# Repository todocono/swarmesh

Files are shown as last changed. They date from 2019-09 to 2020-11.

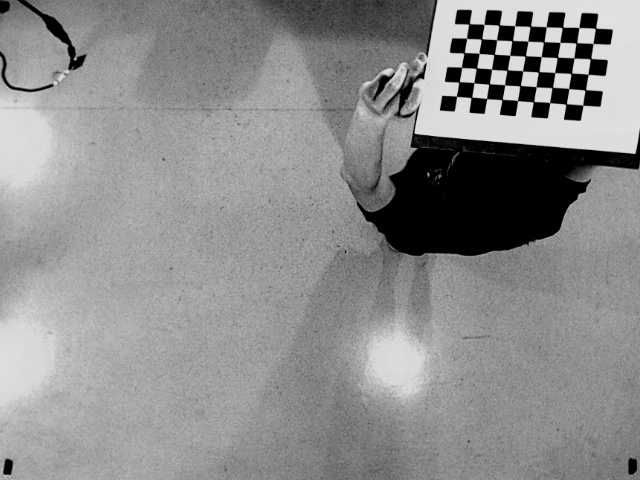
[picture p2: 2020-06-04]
SOFT/testArUco/cam_calib/calib/calib 8.jpg

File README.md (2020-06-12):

# Swarm Mesh Research Team

To read the latest research published by the team, access: 
https://github.com/todocono/DOCS/Publications

To work with the PCB, you will need the latest version of Eagle: https://www.autodesk.com/products/eagle/overview 

To work with the 3D models, you will need Fusion 360 and access the following files:
https://a360.co/2WSIKhr
https://a360.co/2x0crTh

To work with the IDE and latest version, you need:

- Arduino IDE 1.8.9
- CP2102 driver (https://www.silabs.com/products/development-tools/software/usb-to-uart-bridge-vcp-drivers)
- ESP32 Arduino installed 1.0.2 (add https://raw.githubusercontent.com/espressif/arduino-esp32/gh-pages/package_esp32_index.json)
- FastLED library 3.3.2 (from Boards Manager)
- PainlessMesh 1.4.2 (from Boards Manager)
- ArduinoJson 6.12.0 (from Boards Manager)
- TaskScheduler 3.0.2 (from Boards Manager, not really used)
- AsyncTCP (manual install https://github.com/me-no-dev/AsyncTCP)
- AsyncUDP (available in ESP32's arduino library)

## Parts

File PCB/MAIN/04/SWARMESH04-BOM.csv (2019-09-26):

Part | Value | Device | Package | Description | ALLIED_NUMBER | ALLIED_PRICE-STOCK | AVAILABILITY | DESCRIPTION | HEIGHT | MANUFACTURER_NAME | MANUFACTURER_PART_NUMBER | MF | MOUSER_PART_NUMBER | MOUSER_PRICE-STOCK | MP | MPN | OC_FARNELL | OC_NEWARK | PACKAGE | PRICE | RS_PART_NUMBER | RS_PRICE-STOCK | SF_ID
BAT+ |  | PINHD-1X1-BIGPOGO | 1X1-BIGPOGO | Pin header 1x1 for 0.1 spacing"
BAT- |  | PINHD-1X1-BIGPOGO | 1X1-BIGPOGO | Pin header 1x1 for 0.1 spacing"
C1 | 10uF | CPOL-USE2-5 | E2-5 | POLARIZED CAPACITOR, American symbol
C2 |  | C-US025-030X050 | C025-030X050 | CAPACITOR, American symbol
C3 |  | C-US025-025X050 | C025-025X050 | CAPACITOR, American symbol
C4 |  | C-US025-025X050 | C025-025X050 | CAPACITOR, American symbol
C5 |  | C-US025-030X050 | C025-030X050 | CAPACITOR, American symbol
C6 |  | C-US025-025X050 | C025-025X050 | CAPACITOR, American symbol
CHG1+ |  | PINHD-1X1-BIGPOGO | 1X1-BIGPOGO | Pin header 1x1 for 0.1 spacing"
CHG1- |  | PINHD-1X1-BIGPOGO | 1X1-BIGPOGO | Pin header 1x1 for 0.1 spacing"
CHG2+ |  | PINHD-1X1-BIGPOGO | 1X1-BIGPOGO | Pin header 1x1 for 0.1 spacing"
CHG2- |  | PINHD-1X1-BIGPOGO | 1X1-BIGPOGO | Pin header 1x1 for 0.1 spacing"
F1 | RUEF300K-2 | RUEF300K-2 | RUEF300K2 | TE CONNECTIVITY / RAYCHEM - RUEF300K-2 - RESETTABLE FUSE, PTC, 30V, 3A, RADIAL |  |  |  | TE CONNECTIVITY / RAYCHEM - RUEF300K-2 - RESETTABLE FUSE, PTC, 30V, 3A, RADIAL | 16.5mm | TE CONNECTIVITY / RAYCHEM | RUEF300K-2
GPIO25 |  | PINHD-1X3 | 1X03 | PIN HEADER
GPIO26 |  | PINHD-1X3 | 1X03 | PIN HEADER
GPIO32 |  | PINHD-1X3 | 1X03 | PIN HEADER
GPIO33 |  | PINHD-1X3 | 1X03 | PIN HEADER
JI2C |  | PINHD-2X4 | 2X04 | PIN HEADER
JIMU | PINHD-1X10 | PINHD-1X10 | 1X10-BIG | Pin header 1x10 0.1 spacing"
JM1 |  | PINHD-1X6 | 1X06 | PIN HEADER
JM2 |  | PINHD-1X6 | 1X06 | PIN HEADER
JMUX | PINHD-1X10 | PINHD-1X10 | 1X10-BIG | Pin header 1x10 0.1 spacing"
JP1 |  | PINHD-1X1-BIGPOGO | 1X1-BIGPOGO | Pin header 1x1 for 0.1 spacing"
JP2 |  | PINHD-1X1-BIGPOGO | 1X1-BIGPOGO | Pin header 1x1 for 0.1 spacing"
JP3 |  | PINHD-1X1-BIGPOGO | 1X1-BIGPOGO | Pin header 1x1 for 0.1 spacing"
JP4 |  | PINHD-1X1-BIGPOGO | 1X1-BIGPOGO | Pin header 1x1 for 0.1 spacing"
Q1 | TIP122 | TIP122 | TO270P460X1020X2008-3P | TIP122, Darlington Transistor, NPN 8 A 100 V HFE:1000, 3-Pin, TO-220 |  |  |  | TIP122, Darlington Transistor, NPN 8 A 100 V HFE:1000, 3-Pin, TO-220 | 4.6mm | STMicroelectronics | TIP122 |  | 511-TIP122 | https://www.mouser.com/Search/Refine.aspx?Keyword=511-TIP122
R1 | 220 | R-US_0207/9 | 0207/9 | RESISTOR, American symbol
R7 | 1k | R-US_0207/9 | 0207/9 | RESISTOR, American symbol
R8 | 100 | R-US_0207/9 | 0207/9 | RESISTOR, American symbol
R10 | 1k | R-US_0207/9 | 0207/9 | RESISTOR, American symbol
R11 | 100 | R-US_0207/9 | 0207/9 | RESISTOR, American symbol
R14 | 10k | R-US_0207/9 | 0207/9 | RESISTOR, American symbol
R15 | 47k | R-US_0207/9 | 0207/9 | RESISTOR, American symbol
RB | 1k | R-US_0207/9 | 0207/9 | RESISTOR, American symbol
RD | 0 | R-US_0207/9 | 0207/9 | RESISTOR, American symbol
S1 |  | SWITCH_320-938 | PS22F03 | TOGGLE SWITCH
T1 |  | CONN_01SPRING-CONN | SPRING-CONNECTOR | Single connection point. Often used as Generic Header-pin footprint for 0.1 inch spaced/style header connections |  |  |  |  |  |  |  |  |  |  |  |  |  |  |  |  |  |  | PRT-11822
T2 |  | CONN_01SPRING-CONN | SPRING-CONNECTOR | Single connection point. Often used as Generic Header-pin footprint for 0.1 inch spaced/style header connections |  |  |  |  |  |  |  |  |  |  |  |  |  |  |  |  |  |  | PRT-11822
T3 |  | CONN_01SPRING-CONN | SPRING-CONNECTOR | Single connection point. Often used as Generic Header-pin footprint for 0.1 inch spaced/style header connections |  |  |  |  |  |  |  |  |  |  |  |  |  |  |  |  |  |  | PRT-11822
T4 |  | CONN_01SPRING-CONN | SPRING-CONNECTOR | Single connection point. Often used as Generic Header-pin footprint for 0.1 inch spaced/style header connections |  |  |  |  |  |  |  |  |  |  |  |  |  |  |  |  |  |  | PRT-11822
U1 | ESP32DEVKITC | ESP32DEVKITC | ESP32-DEVKITC
U2 | CD4051BEE4 | CD4051BEE4 | CD4051BEE4DIP | Multiplexer 8pin ADC/DAC
U3 | L293D | L293D | DIL16 | PUSH-PULL 4 CHANNEL DRIVER |  |  |  |  |  |  |  |  |  |  |  | L293D | 9589619 | 56P8249
U4 | L7805CV-DG | L7805CV-DG | TO270P460X1020X2008-3P | Voltage Regulator 5V 4% 1.5A TO220 L7805CV-DG, Linear Voltage Regulator, Current Limit, Shut-Down 1.5A 5 V, 3-Pin TO220 | 70390055 | http://www.alliedelec.com/stmicroelectronics-l7805cv-dg/70390055/ |  | Voltage Regulator 5V 4% 1.5A TO220 L7805CV-DG, Linear Voltage Regulator, Current Limit, Shut-Down 1.5A 5 V, 3-Pin TO220 | 4.6mm | STMicroelectronics | L7805CV-DG |  | 511-L7805CV-DG | https://www.mouser.com/Search/Refine.aspx?Keyword=511-L7805CV-DG |  |  |  |  |  |  | 7931346P | http://uk.rs-online.com/web/p/products/7931346P
U5 | TCRT5000L | TCRT5000L | XDCR_TCRT5000L | TCRT5000 Series 940 nm 100 mA 60 mA Transistor Output Reflective Optical Sensor |  |  | Unavailable | TCRT5000 Series 940 nm 100 mA 60 mA Transistor Output Reflective Optical Sensor |  |  |  | Vishay Semiconductor |  |  | TCRT5000L |  |  |  | PCB Mount Vishay | None
U6 | TCRT5000L | TCRT5000L | XDCR_TCRT5000L | TCRT5000 Series 940 nm 100 mA 60 mA Transistor Output Reflective Optical Sensor |  |  | Unavailable | TCRT5000 Series 940 nm 100 mA 60 mA Transistor Output Reflective Optical Sensor |  |  |  | Vishay Semiconductor |  |  | TCRT5000L |  |  |  | PCB Mount Vishay | None

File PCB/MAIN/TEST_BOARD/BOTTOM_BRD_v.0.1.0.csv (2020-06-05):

Part | Value | Device | Package | Description | AVAILABILITY | DESCRIPTION | DIGIKEY-PURCHASE-URL | HEIGHT | MANUFACTURER_NAME | MANUFACTURER_PART_NUMBER | MF | MOUSER_PART_NUMBER | MOUSER_PRICE-STOCK | MP | MPN | OC_FARNELL | OC_NEWARK | PACKAGE | POPULARITY | PRICE | RS_PART_NUMBER | RS_PRICE-STOCK | SPICEPREFIX
BT1 | 3.7V BATT | 6S-AA | BAT_6S-AA |  | Unavailable | BATTERY HOLDER AA PC PIN | https://snapeda.com/shop?store=DigiKey&id=4389101 |  |  |  | MPD |  |  | 6S-AA |  |  |  | None |  | None
C1 |  | C-US025-030X050 | C025-030X050 | CAPACITOR, American symbol
C2 |  | C-US025-025X050 | C025-025X050 | CAPACITOR, American symbol
C3 |  | C-US025-025X050 | C025-025X050 | CAPACITOR, American symbol
F1 | RUEF300K-2 | RUEF300K-2 | RUEF300K2 | TE CONNECTIVITY / RAYCHEM - RUEF300K-2 - RESETTABLE FUSE, PTC, 30V, 3A, RADIAL |  | TE CONNECTIVITY / RAYCHEM - RUEF300K-2 - RESETTABLE FUSE, PTC, 30V, 3A, RADIAL |  | 16.5mm | TE CONNECTIVITY / RAYCHEM | RUEF300K-2
JM1 | B6B-ZR | B6B-ZR | B6B-ZR | JST-ZH Connector | Unavailable | Connector Header Surface Mount 6 position 0.059 _1.50mm_ |  |  |  |  | JST |  |  | B6B-ZR |  |  |  | None |  | None
JM2 | B6B-ZR | B6B-ZR | B6B-ZR | JST-ZH Connector | Unavailable | Connector Header Surface Mount 6 position 0.059 _1.50mm_ |  |  |  |  | JST |  |  | B6B-ZR |  |  |  | None |  | None
L1 | 82114R | 82114R | 82114R | INDUCTOR |  |  |  |  |  |  |  |  |  |  |  |  |  |  | 2 |  |  |  | L
LDOREG | MCP1700T-3302E/TT | MCP1700T-3302E/TT | SOT95P237X112-3N |  | Unavailable | IC REG LINEAR 3.3V 250MA SOT23-3 |  |  |  |  | Microchip Technology |  |  | MCP1700T-3302E/TT |  |  |  | None |  | None
R1 |  | R-US_0207/9 | 0207/9 | RESISTOR, American symbol
R2 |  | R-US_0207/9 | 0207/9 | RESISTOR, American symbol
R3 |  | R-US_0207/9 | 0207/9 | RESISTOR, American symbol
R4 |  | R-US_0207/9 | 0207/9 | RESISTOR, American symbol
S1 |  | SWITCH_320-938 | PS22F03 | TOGGLE SWITCH
U1 | ESP32DEVKITC | ESP32DEVKITC | ESP32-DEVKITC
U2 | L293D | L293D | DIL16 | PUSH-PULL 4 CHANNEL DRIVER |  |  |  |  |  |  |  |  |  |  | L293D | 9589619 | 56P8249

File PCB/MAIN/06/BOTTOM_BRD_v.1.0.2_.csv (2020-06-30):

Part | Value | Device | Package | Description | AVAILABILITY | COMMENT | DESCRIPTION | DIGIKEY-PURCHASE-URL | HEIGHT | MANUFACTURER_NAME | MANUFACTURER_PART_NUMBER | MF | MOUSER_PART_NUMBER | MOUSER_PRICE-STOCK | MP | MPN | OC_FARNELL | OC_NEWARK | PACKAGE | POPULARITY | PRICE | RS_PART_NUMBER | RS_PRICE-STOCK | SF_ID | SPICEPREFIX
BT1 | 3.7V-BAT | 6S-AA | BAT_6S-AA |  | Unavailable |  | BATTERY HOLDER AA PC PIN | https://snapeda.com/shop?store=DigiKey&id=4389101 |  |  |  | MPD |  |  | 6S-AA |  |  |  | None |  | None
C1 | 22uF | C-USC0805 | C0805 | CAPACITOR, American symbol |  |  |  |  |  |  |  |  |  |  |  |  |  |  |  | 63 |  |  |  |  | C
C2 | 22uF | C-USC0805 | C0805 | CAPACITOR, American symbol |  |  |  |  |  |  |  |  |  |  |  |  |  |  |  | 63 |  |  |  |  | C
C3 | 100nF | C-USC0805 | C0805 | CAPACITOR, American symbol |  |  |  |  |  |  |  |  |  |  |  |  |  |  |  | 63 |  |  |  |  | C
C4 | 100uF | CPOL-US153CLV-0605 | 153CLV-0605 | POLARIZED CAPACITOR, American symbol |  |  |  |  |  |  |  |  |  |  |  |  |  |  |  | 8 |  |  |  |  | C
C5 | 22uF | C-USC0805 | C0805 | CAPACITOR, American symbol |  |  |  |  |  |  |  |  |  |  |  |  |  |  |  | 63 |  |  |  |  | C
C6 | 100nF | C-USC0805 | C0805 | CAPACITOR, American symbol |  |  |  |  |  |  |  |  |  |  |  |  |  |  |  | 63 |  |  |  |  | C
C7 | 100nF | C-USC0805 | C0805 | CAPACITOR, American symbol |  |  |  |  |  |  |  |  |  |  |  |  |  |  |  | 63 |  |  |  |  | C
C8 | 100nF | C-USC0805 | C0805 | CAPACITOR, American symbol |  |  |  |  |  |  |  |  |  |  |  |  |  |  |  | 63 |  |  |  |  | C
C9 | 100nF | C-USC0805 | C0805 | CAPACITOR, American symbol |  |  |  |  |  |  |  |  |  |  |  |  |  |  |  | 63 |  |  |  |  | C
C10 | 100nF | C-USC0805 | C0805 | CAPACITOR, American symbol |  |  |  |  |  |  |  |  |  |  |  |  |  |  |  | 63 |  |  |  |  | C
C11 | 100nF | C-USC0805 | C0805 | CAPACITOR, American symbol |  |  |  |  |  |  |  |  |  |  |  |  |  |  |  | 63 |  |  |  |  | C
CHARGING | WS2812B5050 | WS2812B5050 | WS2812B
CHG+ |  | PINHD-1X1-BIGPOGO | 1X1-BIGPOGO | Pin header 1x1 for 0.1 spacing"
CHG- |  | PINHD-1X1-BIGPOGO | 1X1-BIGPOGO | Pin header 1x1 for 0.1 spacing"
D2 | SS14 | SS14 | DO214 |  | Unavailable |  | Diode Schottky 40V 1A Surface Mount SMA (DO-214AC) | https://snapeda.com/shop?store=DigiKey&id=229686 |  |  |  | ON Semiconductor |  |  | SS14 |  |  |  | DO-214AC-214 ON Semiconductor |  | None
F1 | RUEF300K-2 | RUEF300K-2 | RUEF300K2 | TE CONNECTIVITY / RAYCHEM - RUEF300K-2 - RESETTABLE FUSE, PTC, 30V, 3A, RADIAL |  |  | TE CONNECTIVITY / RAYCHEM - RUEF300K-2 - RESETTABLE FUSE, PTC, 30V, 3A, RADIAL |  | 16.5mm | TE CONNECTIVITY / RAYCHEM | RUEF300K-2
I2C |  | PINHD-1X4 | 1X04 | PIN HEADER |  |  |  |  |  |  |  |  |  |  |  |  |  |  |  | 91
IO5 |  | PINHD-1X1 | 1X01 | PIN HEADER |  |  |  |  |  |  |  |  |  |  |  |  |  |  |  | 64
IO15 |  | PINHD-1X1 | 1X01 | PIN HEADER |  |  |  |  |  |  |  |  |  |  |  |  |  |  |  | 64
IO26 |  | PINHD-1X1 | 1X01 | PIN HEADER |  |  |  |  |  |  |  |  |  |  |  |  |  |  |  | 64
IR1 |  | PINHD-1X3 | 1X03 | PIN HEADER
IR2 |  | PINHD-1X3 | 1X03 | PIN HEADER
JM1 | B6B-ZR | B6B-ZR | B6B-ZR | JST-ZH Connector | Unavailable |  | Connector Header Surface Mount 6 position 0.059 _1.50mm_ |  |  |  |  | JST |  |  | B6B-ZR |  |  |  | None |  | None
JM2 | B6B-ZR | B6B-ZR | B6B-ZR | JST-ZH Connector | Unavailable |  | Connector Header Surface Mount 6 position 0.059 _1.50mm_ |  |  |  |  | JST |  |  | B6B-ZR |  |  |  | None |  | None
L1 | 47uH | SDR0604-100KL | INDP5858X480N | Inductor Power Wirewound 120uH 10% 1KHz 22Q-Factor Ferrite 480mA 930mOhm DCR T/R | Unavailable |  | 10µH Unshielded Wirewound Inductor Nonstandard |  |  |  |  | Bourns |  |  | SDR0604-100KL |  |  |  | Nonstandard Bourns |  | None
LED1 |  | LED5MM | LED5MM | LED
LED2 |  | LED5MM | LED5MM | LED
LED3 |  | LED5MM | LED5MM | LED
LED4 |  | LED5MM | LED5MM | LED
LED5 |  | LED5MM | LED5MM | LED
LED6 |  | LED5MM | LED5MM | LED
LED7 |  | LED5MM | LED5MM | LED
LED8 |  | LED5MM | LED5MM | LED
LED9 |  | LED5MM | LED5MM | LED
LED10 |  | LED5MM | LED5MM | LED
PROGRAMMER |  | PINHD-2X6 | 2X06 | PIN HEADER |  |  |  |  |  |  |  |  |  |  |  |  |  |  |  | 8
Q1 | SS8050 | BC850 | SOT23 | NPN TRANSISTOR |  |  |  |  |  |  |  |  |  |  |  |  |  |  |  | 0
Q2 | SS8050 | BC850 | SOT23 | NPN TRANSISTOR |  |  |  |  |  |  |  |  |  |  |  |  |  |  |  | 0
Q3 | TIP122 | TIP122 | TO270P460X1020X2008-3P | TIP122, Darlington Transistor, NPN 8 A 100 V HFE:1000, 3-Pin, TO-220 |  |  | TIP122, Darlington Transistor, NPN 8 A 100 V HFE:1000, 3-Pin, TO-220 |  | 4.6mm | STMicroelectronics | TIP122 |  | 511-TIP122 | https://www.mouser.com/Search/Refine.aspx?Keyword=511-TIP122
R1 | 10k | R-US_M0805 | M0805 | RESISTOR, American symbol |  |  |  |  |  |  |  |  |  |  |  |  |  |  |  | 45 |  |  |  |  | R
R2 | 47k | R-US_M0805 | M0805 | RESISTOR, American symbol |  |  |  |  |  |  |  |  |  |  |  |  |  |  |  | 45 |  |  |  |  | R
R3 | 10k | R-US_M0805 | M0805 | RESISTOR, American symbol |  |  |  |  |  |  |  |  |  |  |  |  |  |  |  | 45 |  |  |  |  | R
R4 | 10k | R-US_M0805 | M0805 | RESISTOR, American symbol |  |  |  |  |  |  |  |  |  |  |  |  |  |  |  | 45 |  |  |  |  | R
R5 | 10k | R-US_M0805 | M0805 | RESISTOR, American symbol |  |  |  |  |  |  |  |  |  |  |  |  |  |  |  | 45 |  |  |  |  | R
R6 | 10k | R-US_M0805 | M0805 | RESISTOR, American symbol |  |  |  |  |  |  |  |  |  |  |  |  |  |  |  | 45 |  |  |  |  | R
R7 | 10k | R-US_M0805 | M0805 | RESISTOR, American symbol |  |  |  |  |  |  |  |  |  |  |  |  |  |  |  | 45 |  |  |  |  | R
R8 | 10k | R-US_M0805 | M0805 | RESISTOR, American symbol |  |  |  |  |  |  |  |  |  |  |  |  |  |  |  | 45 |  |  |  |  | R
R9 | 10k | R-US_M0805 | M0805 | RESISTOR, American symbol |  |  |  |  |  |  |  |  |  |  |  |  |  |  |  | 45 |  |  |  |  | R
R14 | 47 | R-US_M0805 | M0805 | RESISTOR, American symbol |  |  |  |  |  |  |  |  |  |  |  |  |  |  |  | 45 |  |  |  |  | R
R15 | 47 | R-US_M0805 | M0805 | RESISTOR, American symbol |  |  |  |  |  |  |  |  |  |  |  |  |  |  |  | 45 |  |  |  |  | R
R16 | 47 | R-US_M0805 | M0805 | RESISTOR, American symbol |  |  |  |  |  |  |  |  |  |  |  |  |  |  |  | 45 |  |  |  |  | R
R17 | 47 | R-US_M0805 | M0805 | RESISTOR, American symbol |  |  |  |  |  |  |  |  |  |  |  |  |  |  |  | 45 |  |  |  |  | R
R18 | 47 | R-US_M0805 | M0805 | RESISTOR, American symbol |  |  |  |  |  |  |  |  |  |  |  |  |  |  |  | 45 |  |  |  |  | R
R19 | 10k | R-US_M0805 | M0805 | RESISTOR, American symbol |  |  |  |  |  |  |  |  |  |  |  |  |  |  |  | 45 |  |  |  |  | R
R20 | 10k | R-US_M0805 | M0805 | RESISTOR, American symbol |  |  |  |  |  |  |  |  |  |  |  |  |  |  |  | 45 |  |  |  |  | R
R21 | 10k | R-US_M0805 | M0805 | RESISTOR, American symbol |  |  |  |  |  |  |  |  |  |  |  |  |  |  |  | 45 |  |  |  |  | R
R22 | 10k | R-US_M0805 | M0805 | RESISTOR, American symbol |  |  |  |  |  |  |  |  |  |  |  |  |  |  |  | 45 |  |  |  |  | R
R23 | 10k | R-US_M0805 | M0805 | RESISTOR, American symbol |  |  |  |  |  |  |  |  |  |  |  |  |  |  |  | 45 |  |  |  |  | R
RB | 1k | R-US_M0805 | M0805 | RESISTOR, American symbol |  |  |  |  |  |  |  |  |  |  |  |  |  |  |  | 45 |  |  |  |  | R
S1 | 2-1437565-9 | 2-1437565-9 | SW_2-1437565-9 |  | Unavailable | 2-1437565-9 | Tactile Switch SPST-NO Top Actuated Surface Mount |  |  |  |  | TE Connectivity |  |  | 2-1437565-9 |  |  |  | SMD-6 Omron Electronics |  | None
STATE | WS2812B5050 | WS2812B5050 | WS2812B
SW1 | CS12ANW03 | CS12ANW03 | CS12ANW03 |  | Unavailable |  | Slide Switch SPDT Through Hole | https://snapeda.com/shop?store=DigiKey&id=478299 |  |  |  | NKK Switches |  |  | CS12ANW03 |  |  |  | None |  | None
T1 |  | CONN_01SPRING-CONN | SPRING-CONNECTOR | Single connection point. Often used as Generic Header-pin footprint for 0.1 inch spaced/style header connections |  |  |  |  |  |  |  |  |  |  |  |  |  |  |  |  |  |  |  | PRT-11822
T2 |  | CONN_01SPRING-CONN | SPRING-CONNECTOR | Single connection point. Often used as Generic Header-pin footprint for 0.1 inch spaced/style header connections |  |  |  |  |  |  |  |  |  |  |  |  |  |  |  |  |  |  |  | PRT-11822
U1 | ESP32-WROOM-32D | ESP32-WROOM-32D | MODULE_ESP32-WROOM-32D | Bluetooth, WiFi 802.11b/g/n, Bluetooth v4.2 + EDR, Class 1, 2 and 3 Transceiver Module 2.4GHz ~ 2.5GHz Integrated, Trace Surface Mount | Unavailable |  | Bluetooth, WiFi 802.11b/g/n, Bluetooth v4.2 +EDR, Class 1, 2 and 3 Transceiver Module 2.4GHz ~ 2.5GHz Integrated, Trace Surface Mount |  |  |  |  | Espressif Systems |  |  | ESP32-WROOM-32D |  |  |  | Module Espressif Systems |  | None
U2 | L293D | L293D | DIL16 | PUSH-PULL 4 CHANNEL DRIVER |  |  |  |  |  |  |  |  |  |  |  | L293D | 9589619 | 56P8249
U3 | AP2112K-3.3 | AP2112K-3.3TRG1 | SOT95P285X140-5N | AP2112 Series 0.6 A 3.3 V Fixed Output SMT LDO Linear Regulator - SOT23-5 | Unavailable |  | Linear Voltage Regulator IC 1 Output 600mA SOT-25 |  |  |  |  | Diodes Inc. |  |  | AP2112K-3.3TRG1 |  |  |  | SOT-753 Diodes Inc. |  | None
U4 | CE8301 | MCP1702T-3302E/MB | REG_MCP1702T-3302E/MB | MCP1702 Series 250 mA 3.3 V Fixed Output Surface Mount LDO Regulator - SOT-89 | Unavailable |  | Linear Voltage Regulator IC 1 Output 250mA SOT-89-3 |  |  |  |  | Microchip |  |  | MCP1702T-3302E/MB |  |  |  | SOT-89 Microchip |  | None

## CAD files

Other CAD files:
MECH/3D Models/01/Assembly.f3d
MECH/3D Models/01/Base.f3d
MECH/3D Models/01/Emitter Cone.f3d
MECH/3D Models/01/LED Holder.f3d
MECH/3D Models/01/Receiver Plate.f3d

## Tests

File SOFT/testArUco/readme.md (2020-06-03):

# arUco track demo

## intro
this is a demo of aruco tracking.

## steps

1. take 15 to 20 pictures of the calibration chessboard. The chessboard img is in the cam_calib folder.
2. put the photos in the cam_calib/calib folder.
3. run marker_detect.py

## credits
Zander Mao coded (with tutorials help)
Rodolfo Cossovich refined the measurement of distances

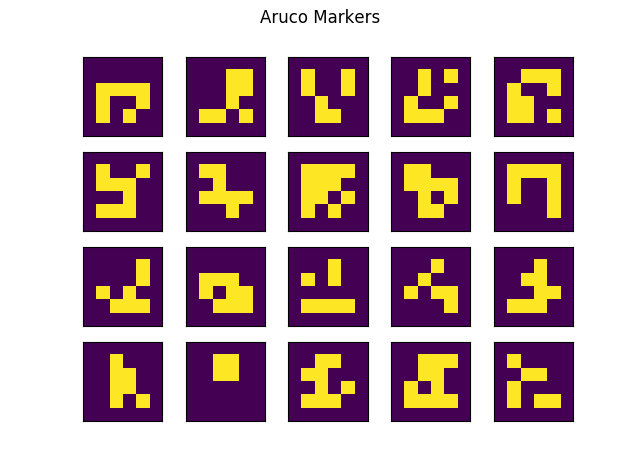
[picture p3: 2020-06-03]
SOFT/testArUco/original/4x4_markers/Figure_1.png

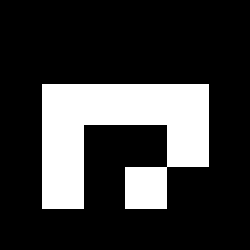
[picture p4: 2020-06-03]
SOFT/testArUco/4x4_markers/img_screenshot_19.01.2019.png

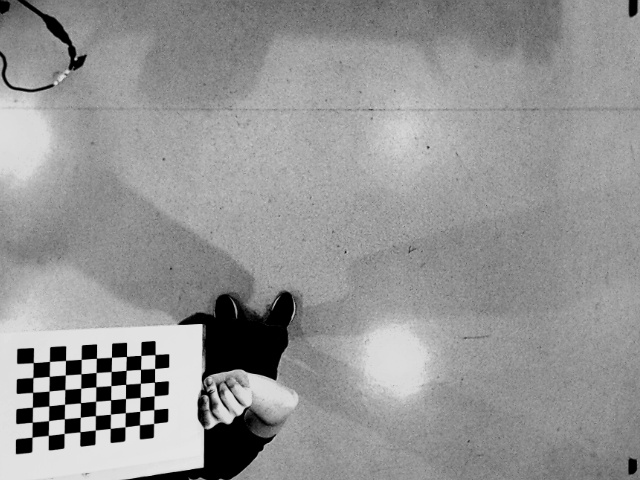
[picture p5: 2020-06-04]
SOFT/testArUco/cam_calib/calib/calib 6.jpg

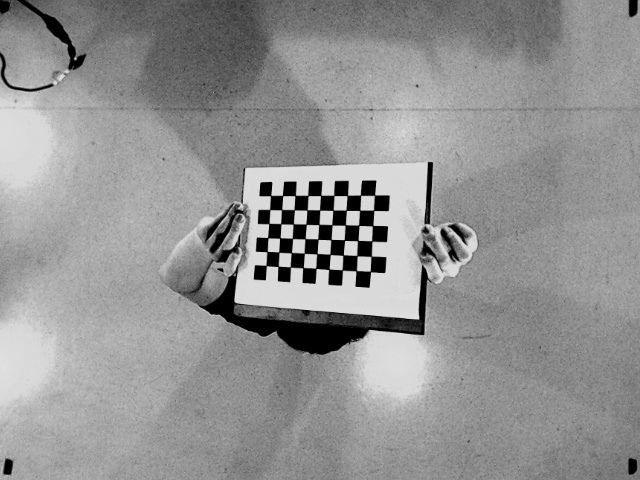
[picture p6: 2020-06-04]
SOFT/testArUco/cam_calib/calib/calib 13.jpg

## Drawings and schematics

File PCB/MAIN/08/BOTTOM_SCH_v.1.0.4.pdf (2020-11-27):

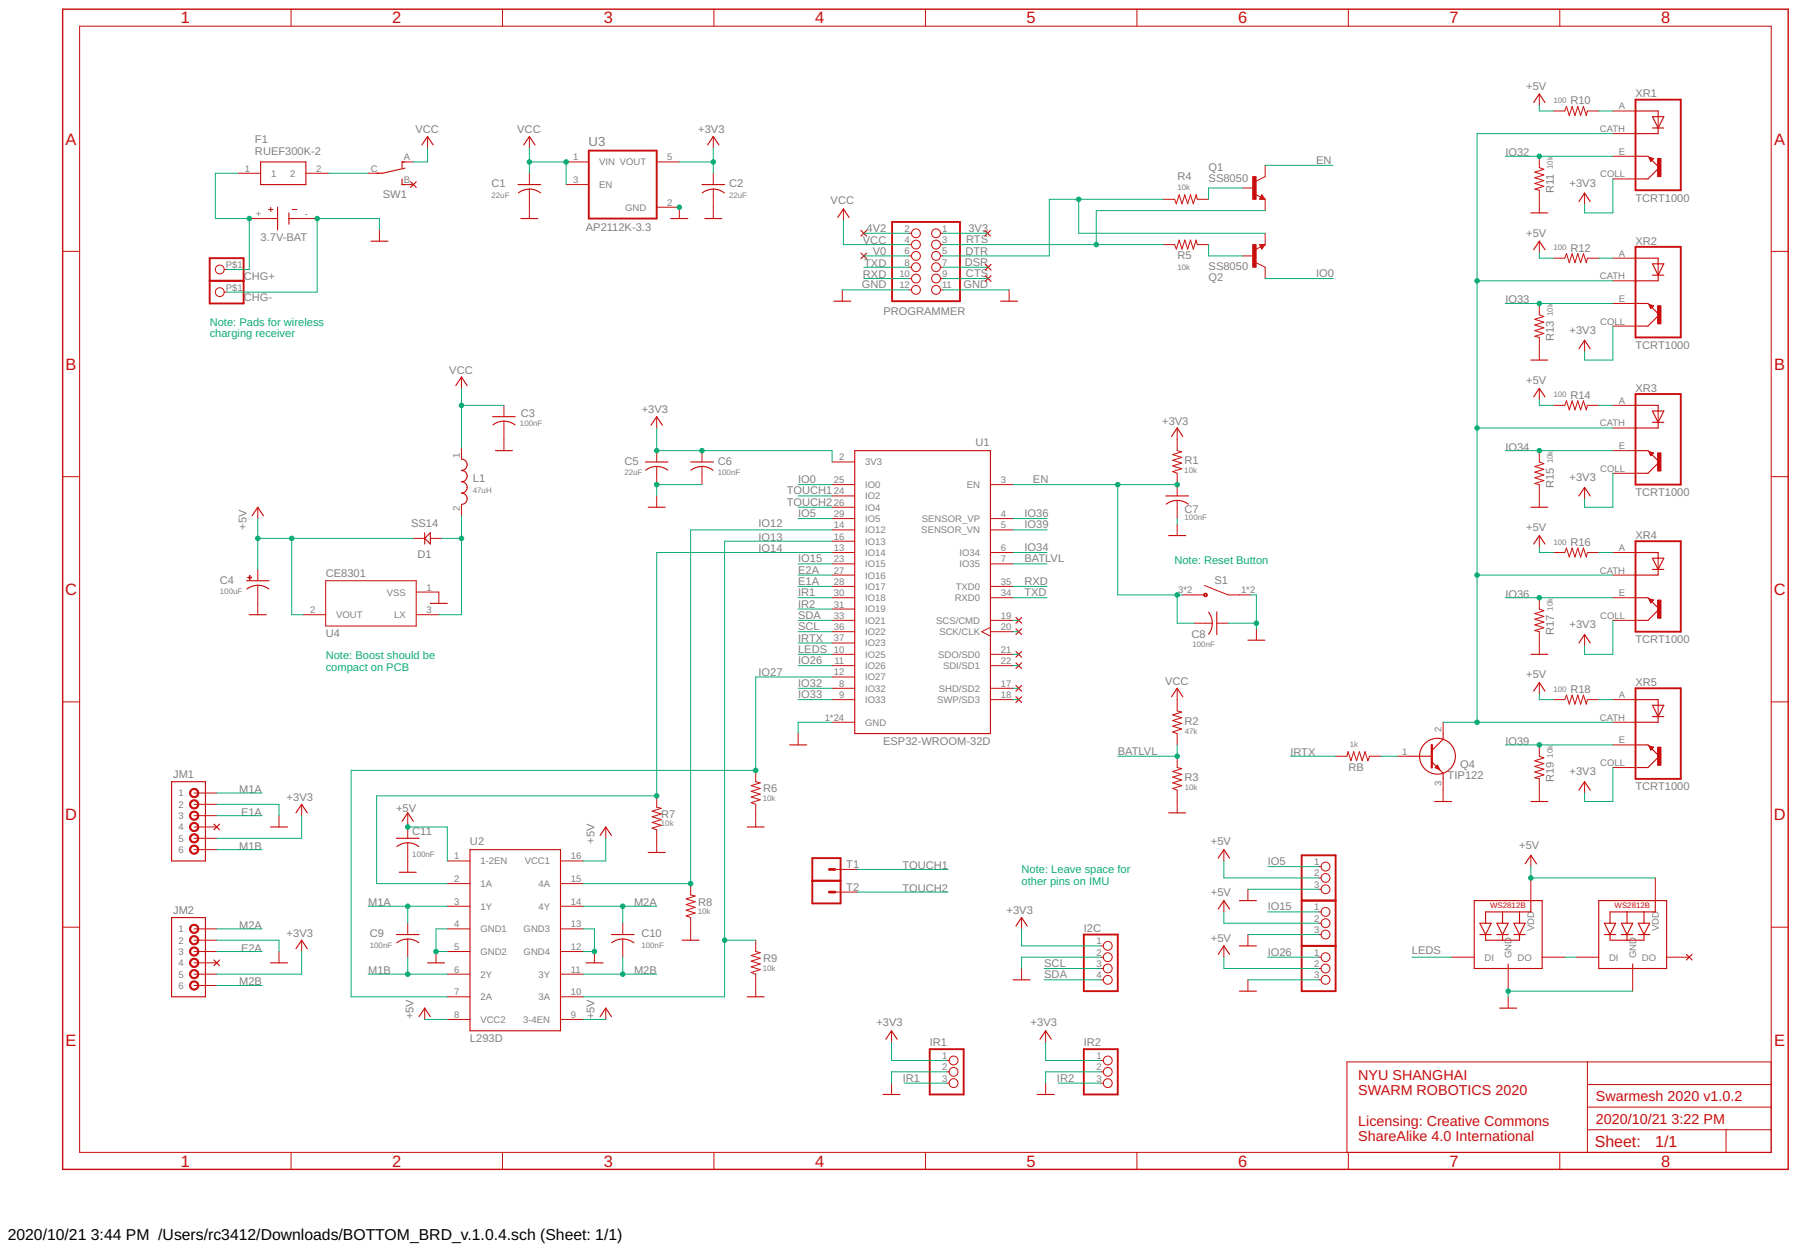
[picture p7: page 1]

Note: Pads for wireless
charging receiver

Note: Boost should be
compact on PCB

Note: Leave space for other pins on IMU

NYU SHANGHAI SWARM ROBOTICS 2020 Licensing: Creative Commons ShareAlike 4.0 International

Sheet: 1/1

2020/10/21 3:44 PM /Users/rc3412/Downloads/BOTTOM_BRD_v.1.0.4.sch (Sheet: 1/1)

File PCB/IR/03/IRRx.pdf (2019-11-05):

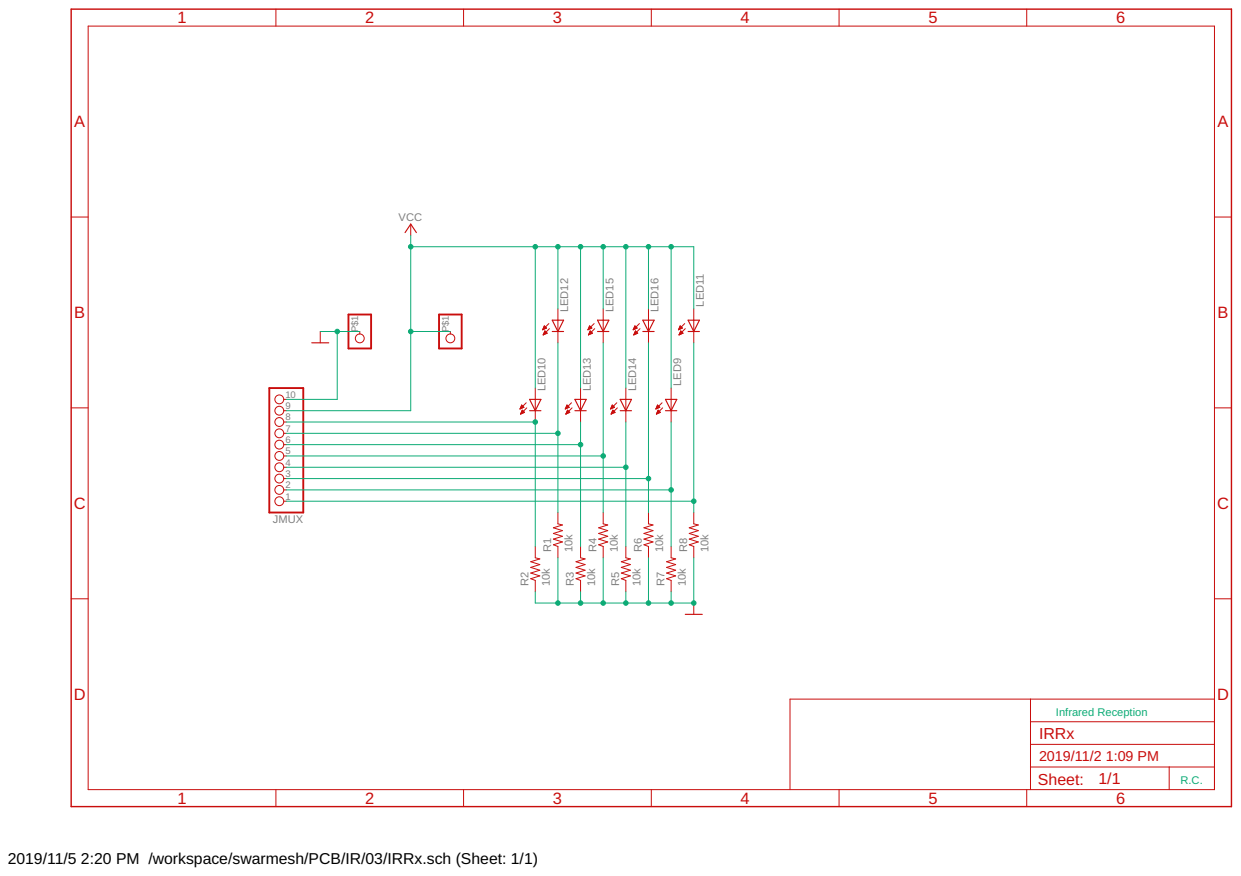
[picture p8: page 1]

2019/11/5 2:20 PM /workspace/swarmesh/PCB/IR/03/IRRx.sch (Sheet: 1/1)

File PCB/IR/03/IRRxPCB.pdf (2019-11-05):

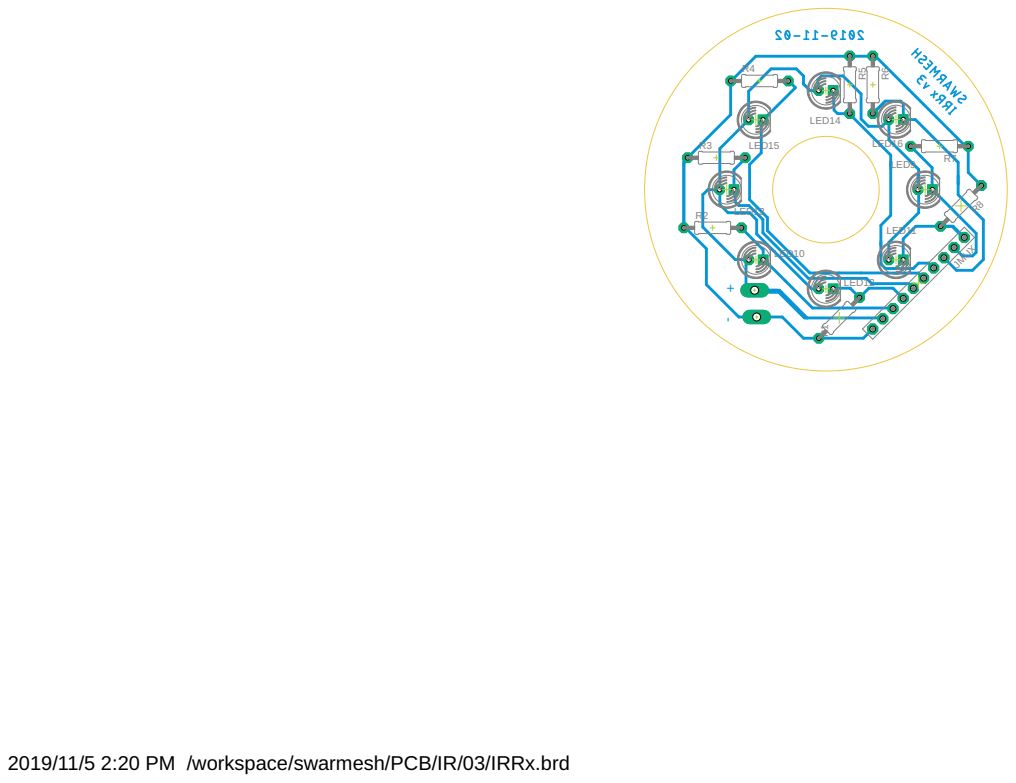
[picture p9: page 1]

2019/11/5 2:20 PM /workspace/swarmesh/PCB/IR/03/IRRx.brd

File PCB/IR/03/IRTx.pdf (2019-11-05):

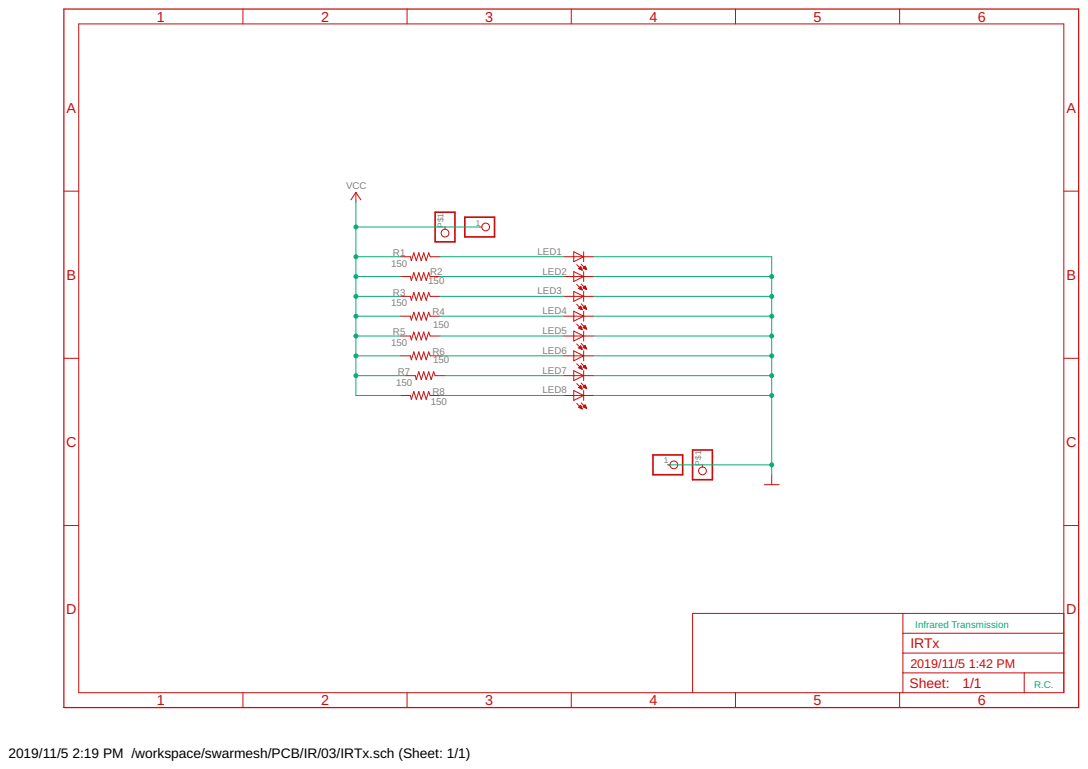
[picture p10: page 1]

2019/11/5 2:19 PM /workspace/swarmesh/PCB/IR/03/IRTx.sch (Sheet: 1/1)

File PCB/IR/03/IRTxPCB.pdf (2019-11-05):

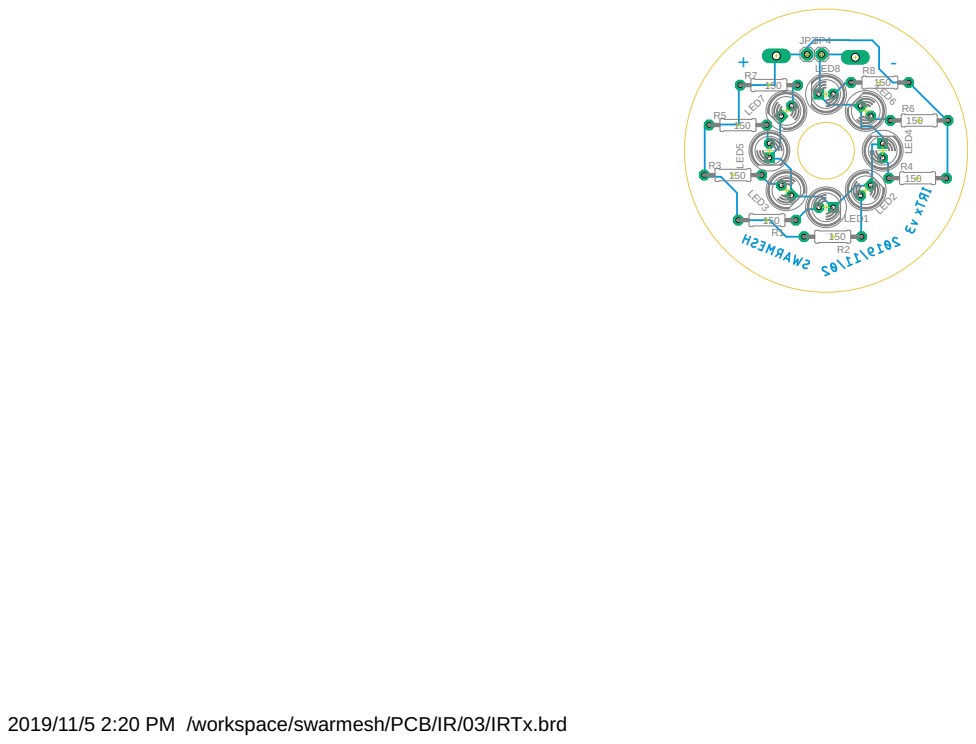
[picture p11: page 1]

2019/11/5 2:20 PM /workspace/swarmesh/PCB/IR/03/IRTx.brd

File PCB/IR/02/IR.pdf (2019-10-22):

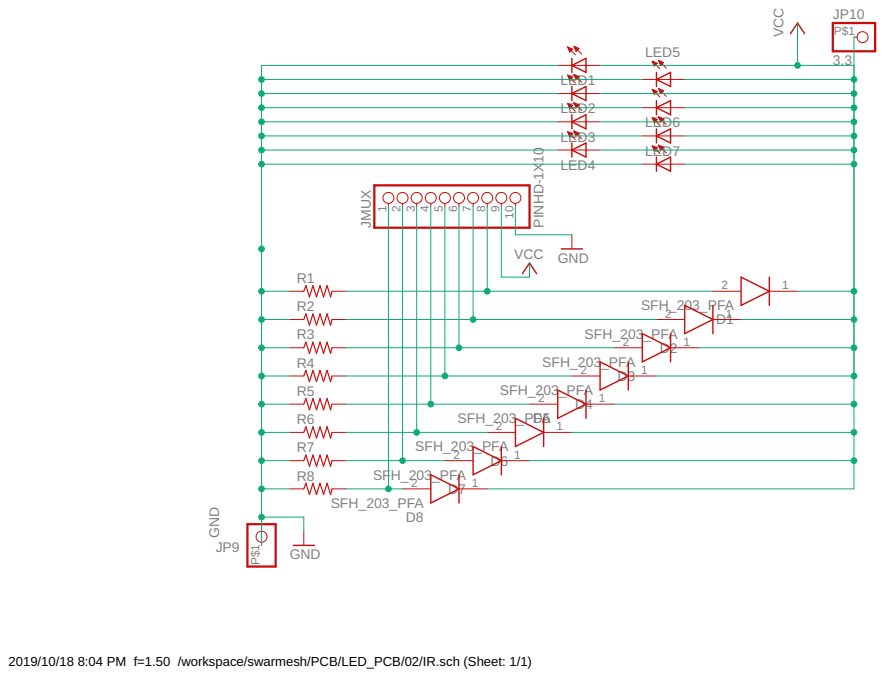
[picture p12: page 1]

2019/10/18 8:04 PM f=1.50 /workspace/swarmesh/PCB/LED_PCB/02/IR.sch (Sheet: 1/1)

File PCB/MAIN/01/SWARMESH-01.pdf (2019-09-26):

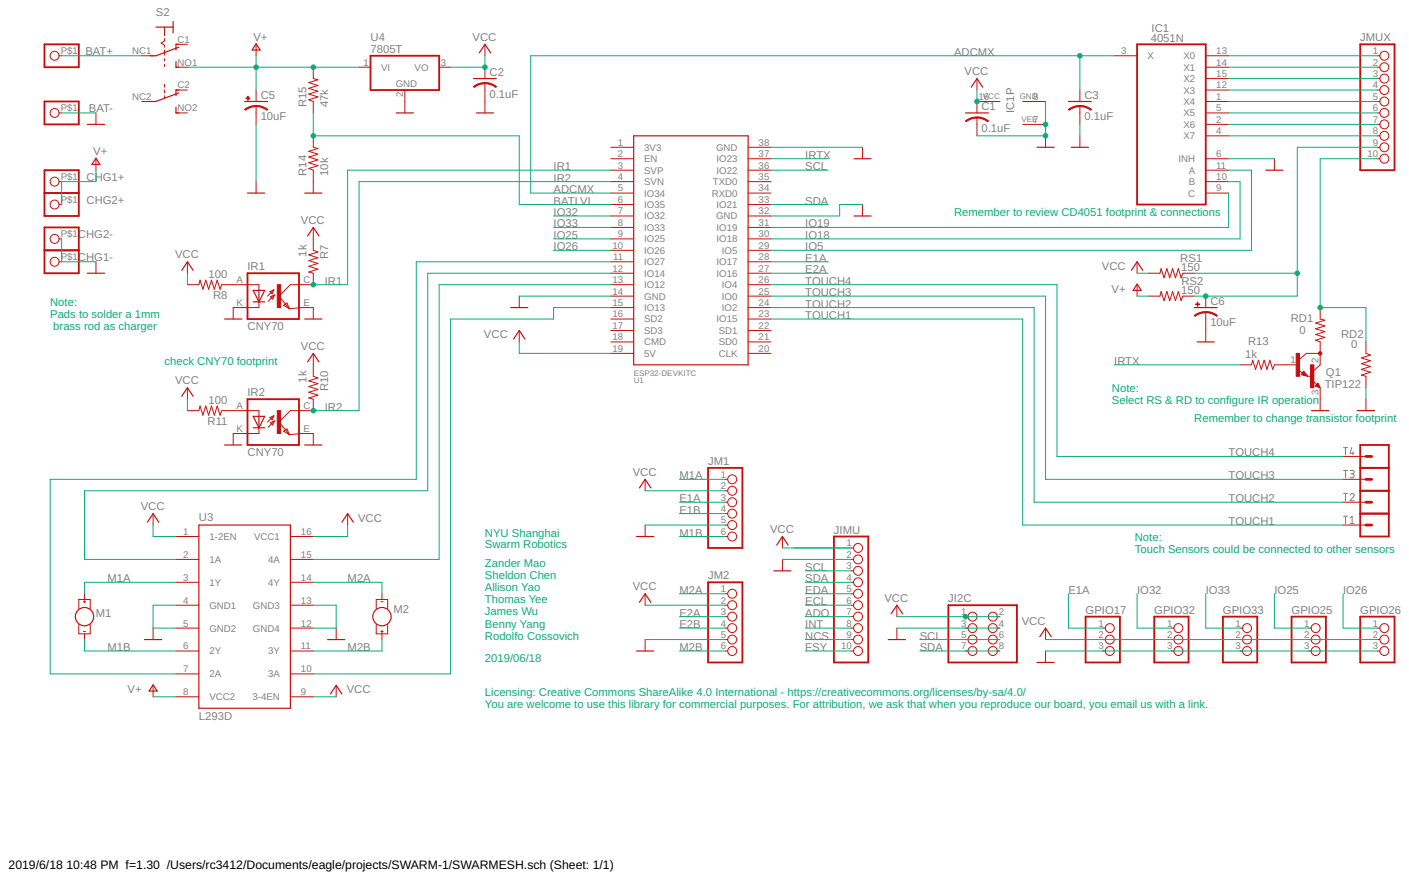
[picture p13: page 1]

Remember to review CD4051 footprint & connections

14 | 25 TOUCH3
15 | 24 TOUCH2

Note:
Pads to solder a 1mm
brass rod as charger

Select RS & RD to configure IR operation

Remember to change transistor footprint

Touch Sensors could be connected to other sensors

Licensing: Creative Commons ShareAlike 4.0 International - https://creativecommons.org/licenses/by-sa/4.0/
You are welcome to use this library for commercial purposes. For attribution, we ask that when you reproduce our board, you email us with a link.

2019/6/18 10:48 PM f=1.30 /Users/rc3412/Documents/eagle/projects/SWARM-1/SWARMESH.sch (Sheet: 1/1)

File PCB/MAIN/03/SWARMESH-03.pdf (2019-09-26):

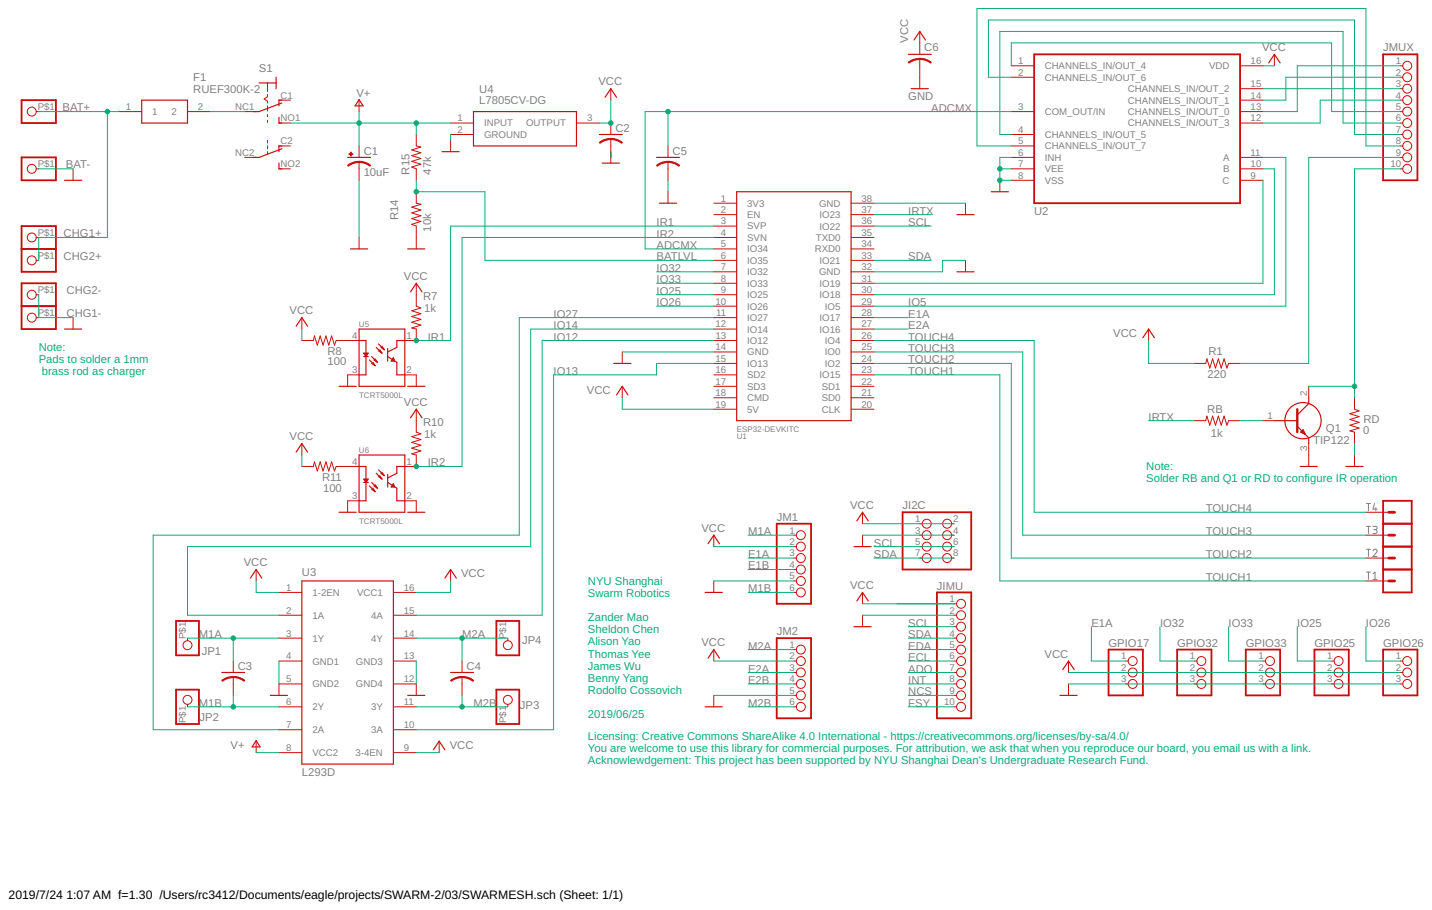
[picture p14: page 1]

IR2 4
ADCMX 5

Note:
Pads to solder a 1mm
brass rod as charger

15 | 24 TOUCH2
16 | 23 TOUCH1

Solder RB and Q1 or RD to configure IR operation

NYU Shanghai
Swarm Robotics
Zander Mao
Sheldon Chen
Alison Yao
Thomas Yee
James Wu
Benny Yang
Rodolfo Cossovich
Licensing: Creative Commons ShareAlike 4.0 International - https://creativecommons.org/licenses/by-sa/4.0/
You are welcome to use this library for commercial purposes. For attribution, we ask that when you reproduce our board, you email us with a link. Acknowlewdgement: This project has been supported by NYU Shanghai Dean's Undergraduate Research Fund.

2019/7/24 1:07 AM f=1.30 /Users/rc3412/Documents/eagle/projects/SWARM-2/03/SWARMESH.sch (Sheet: 1/1)

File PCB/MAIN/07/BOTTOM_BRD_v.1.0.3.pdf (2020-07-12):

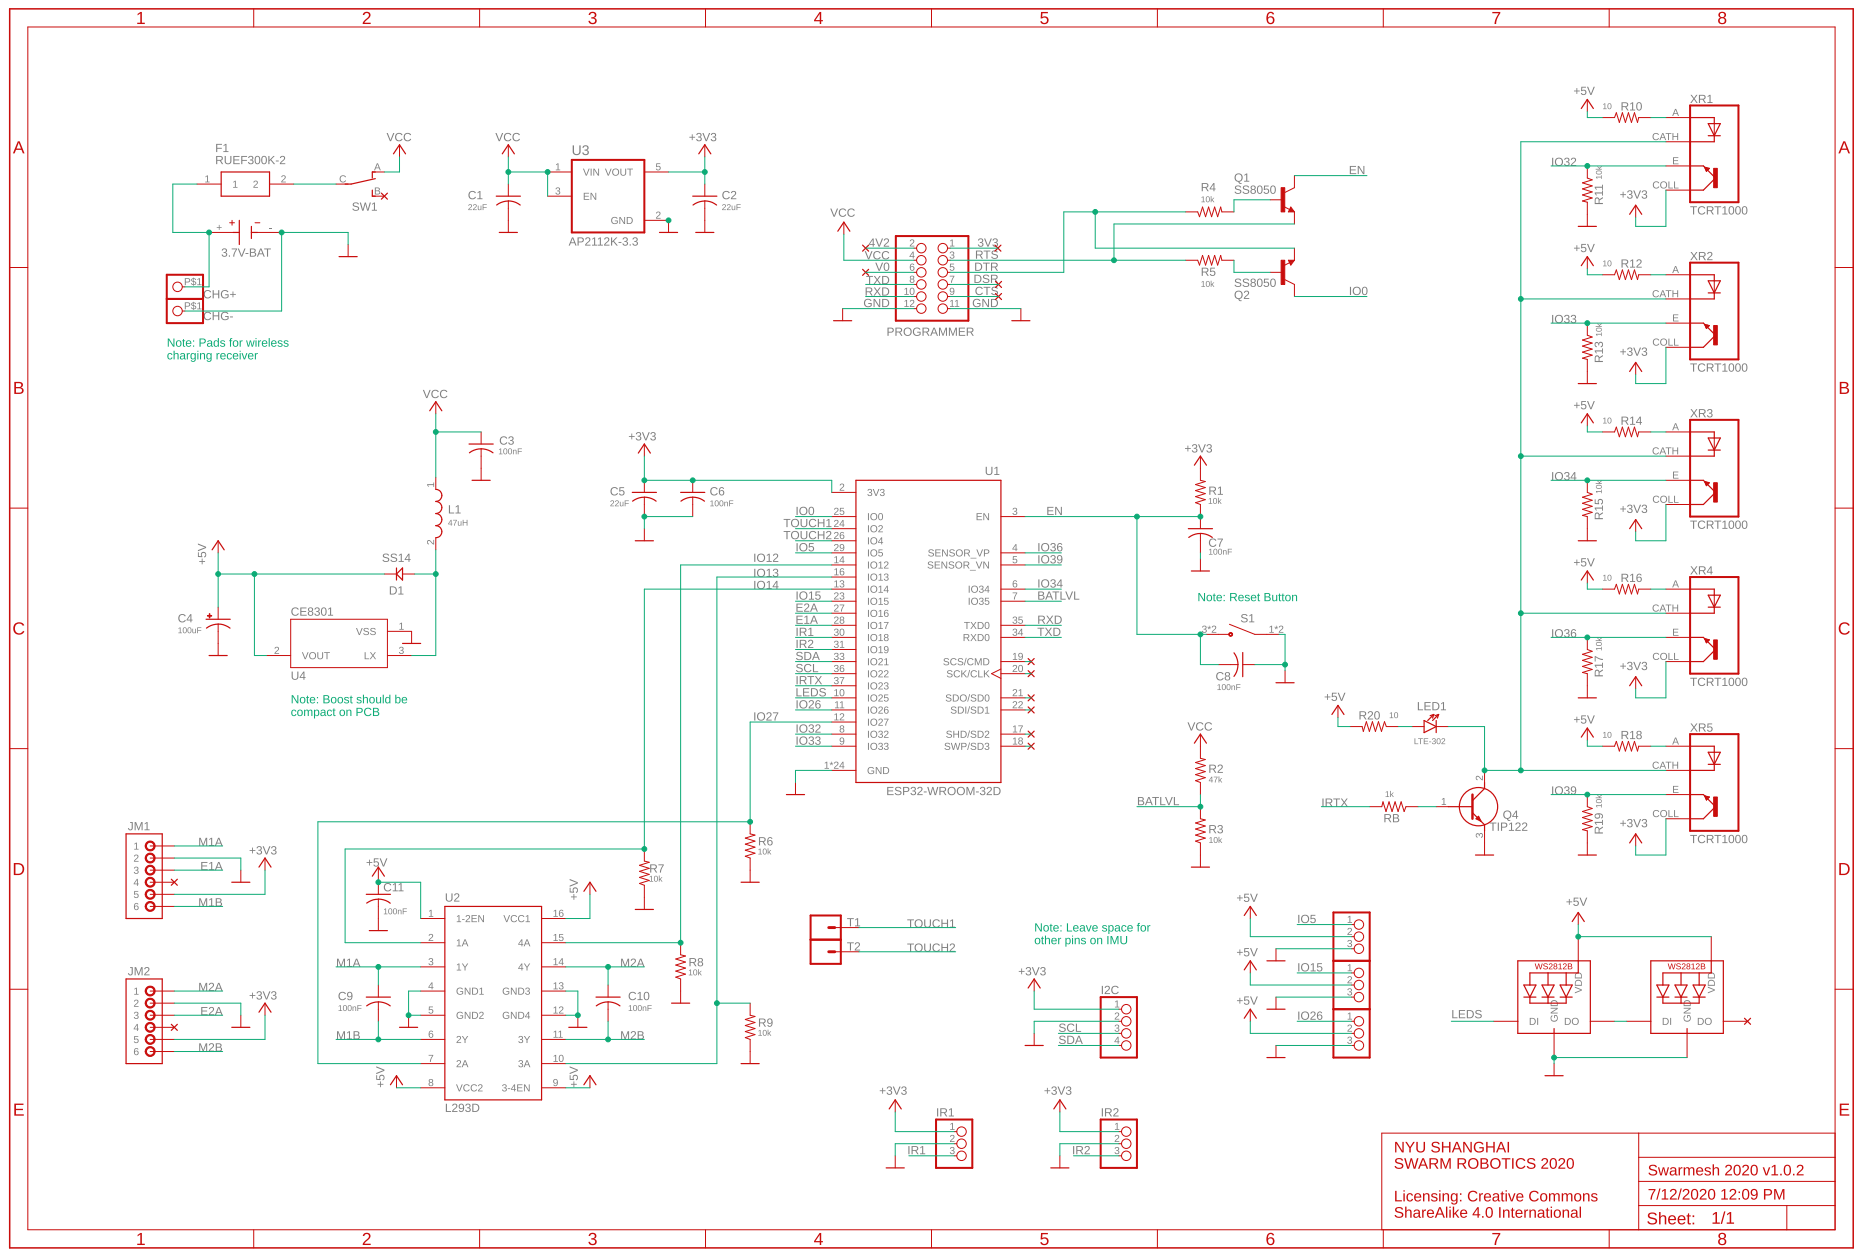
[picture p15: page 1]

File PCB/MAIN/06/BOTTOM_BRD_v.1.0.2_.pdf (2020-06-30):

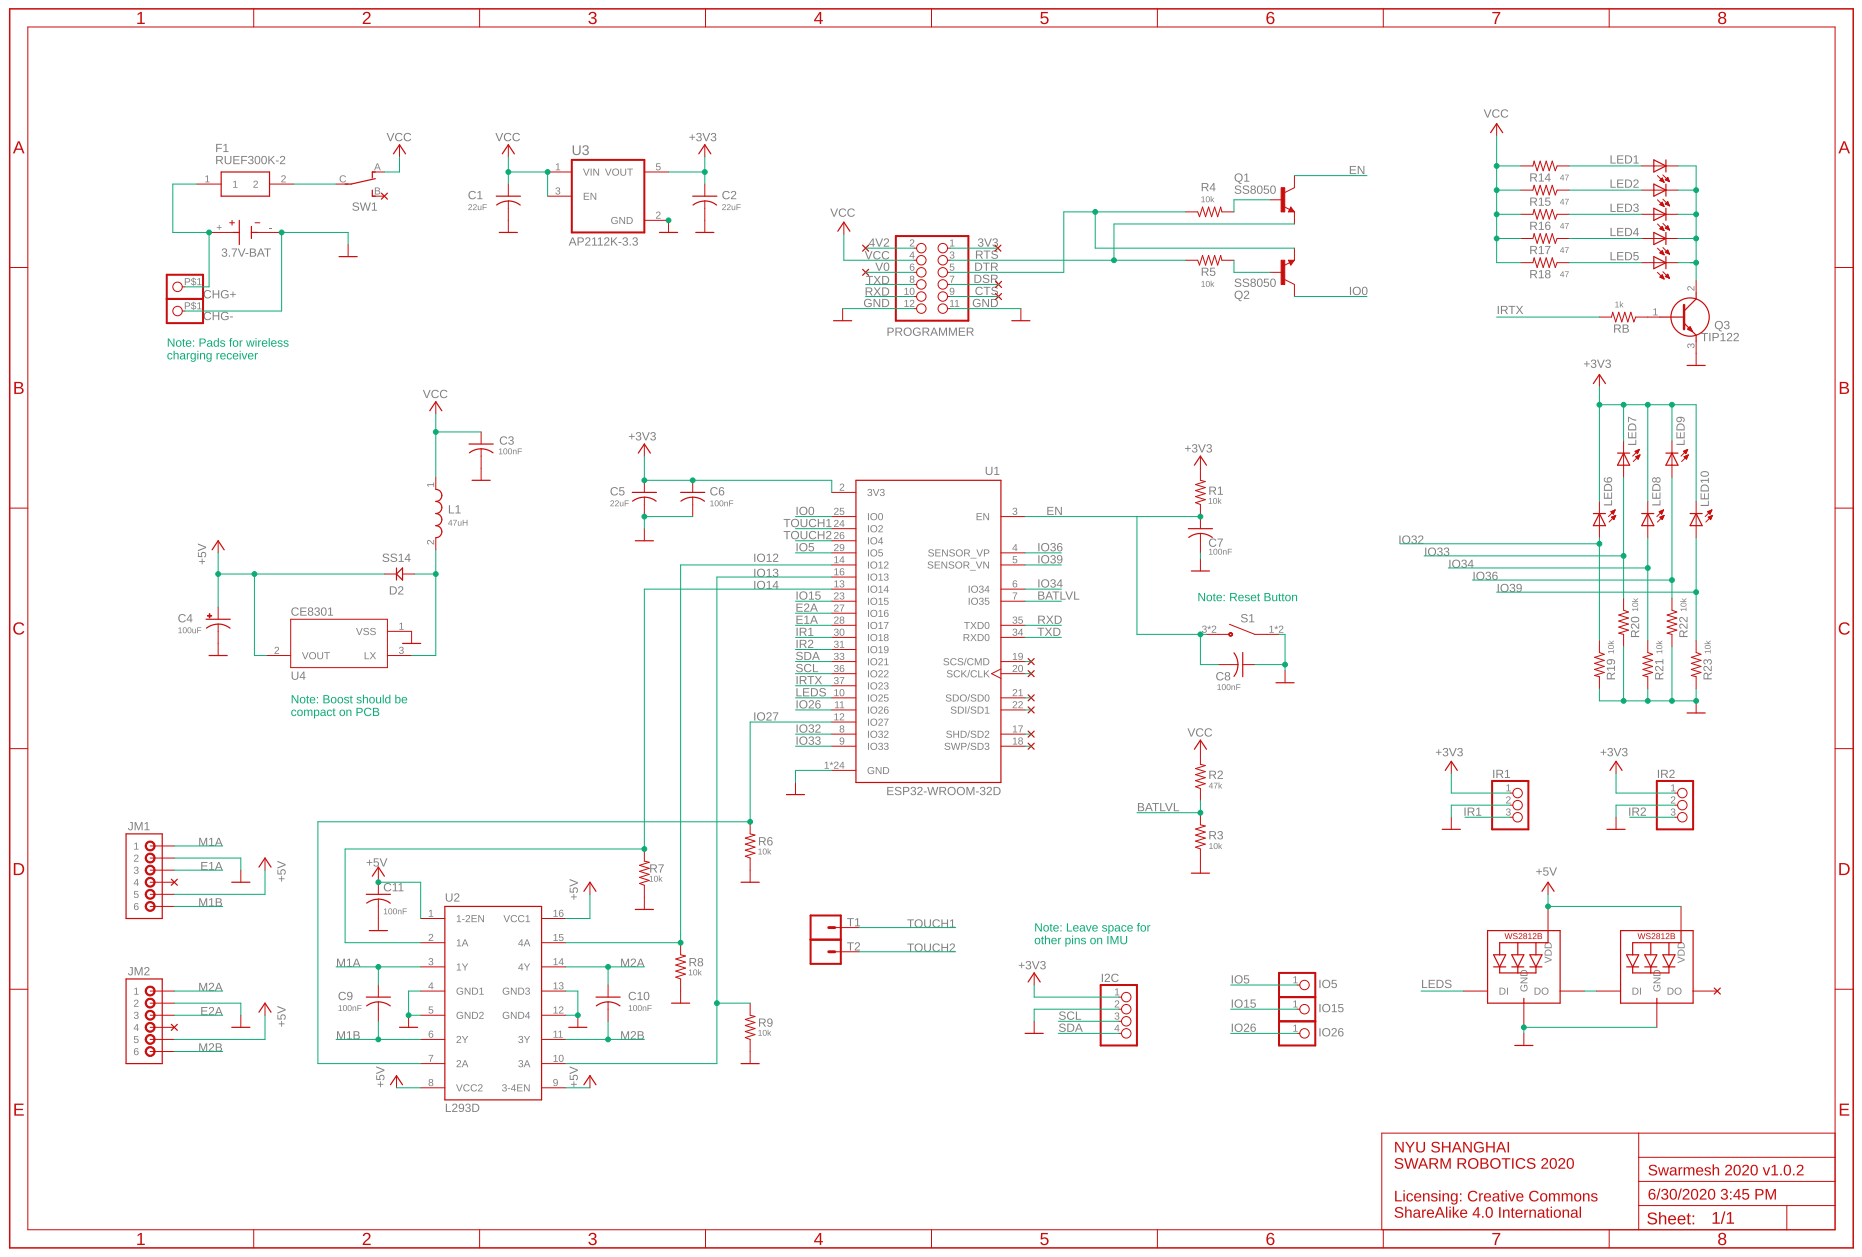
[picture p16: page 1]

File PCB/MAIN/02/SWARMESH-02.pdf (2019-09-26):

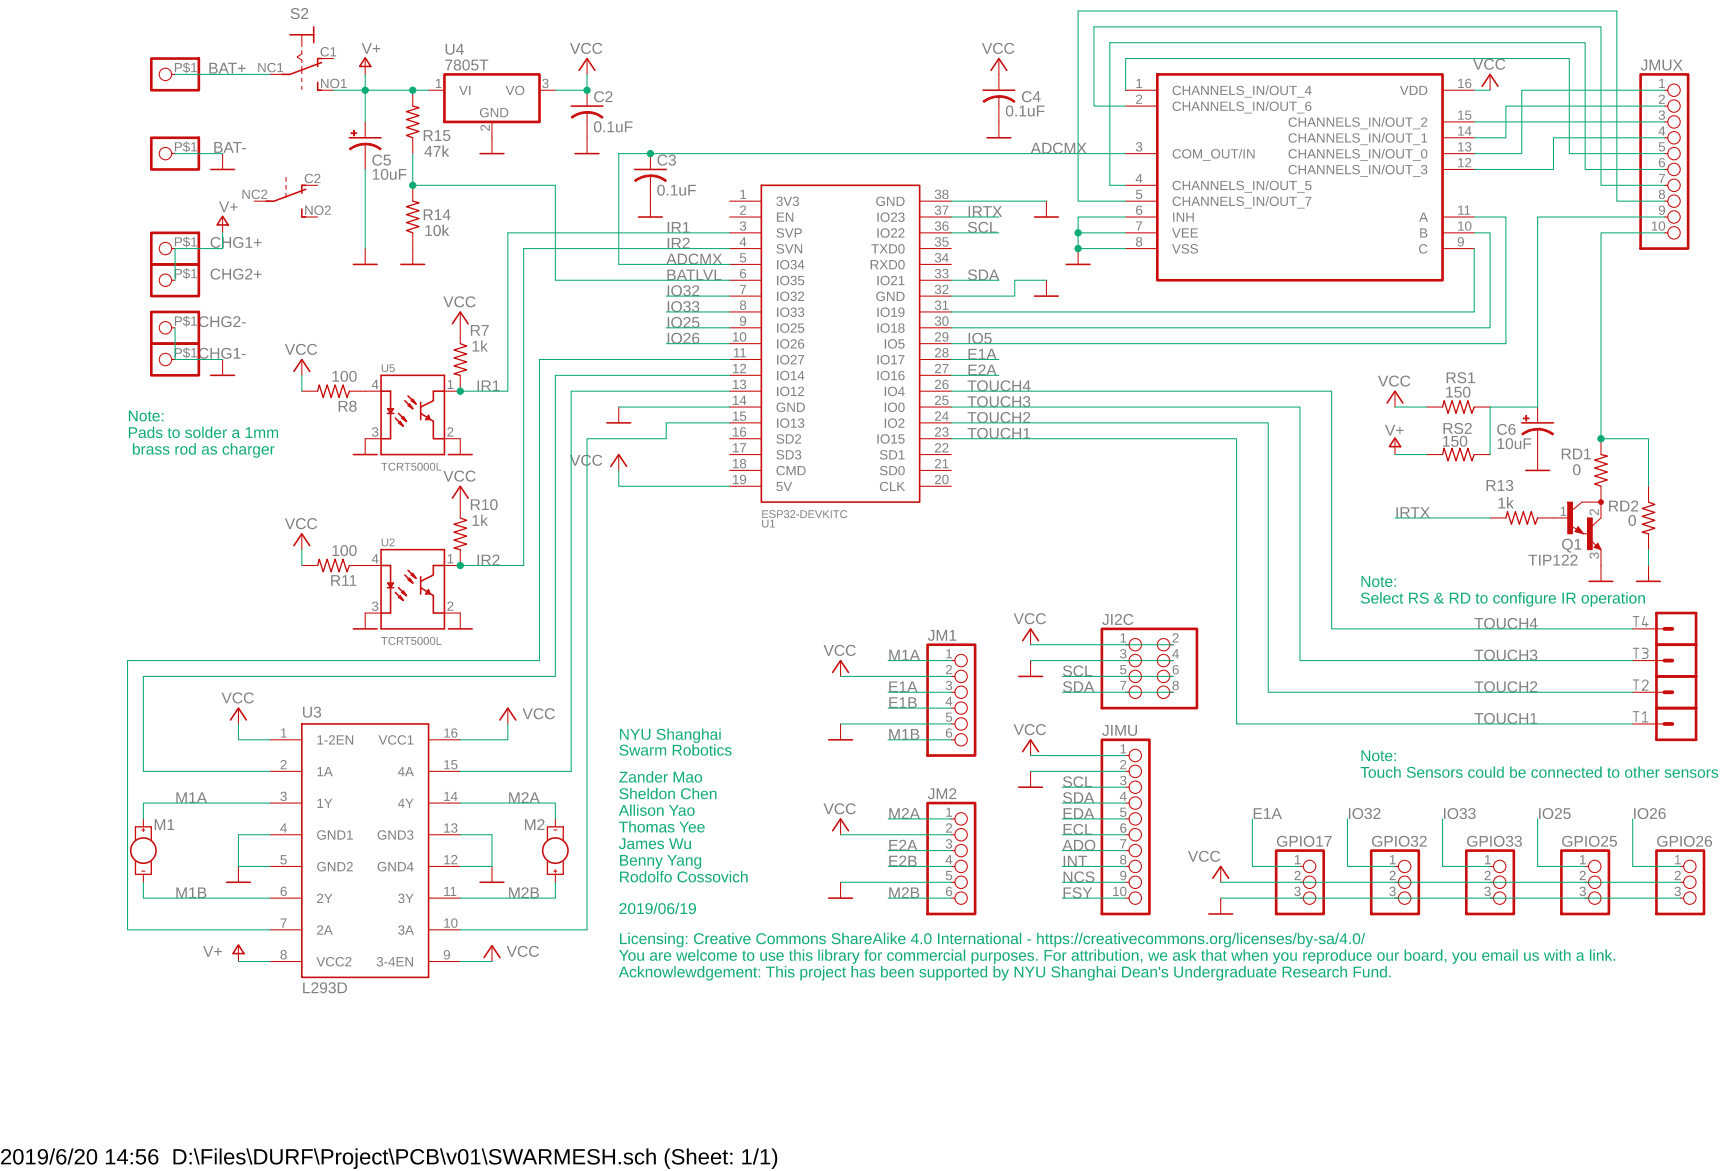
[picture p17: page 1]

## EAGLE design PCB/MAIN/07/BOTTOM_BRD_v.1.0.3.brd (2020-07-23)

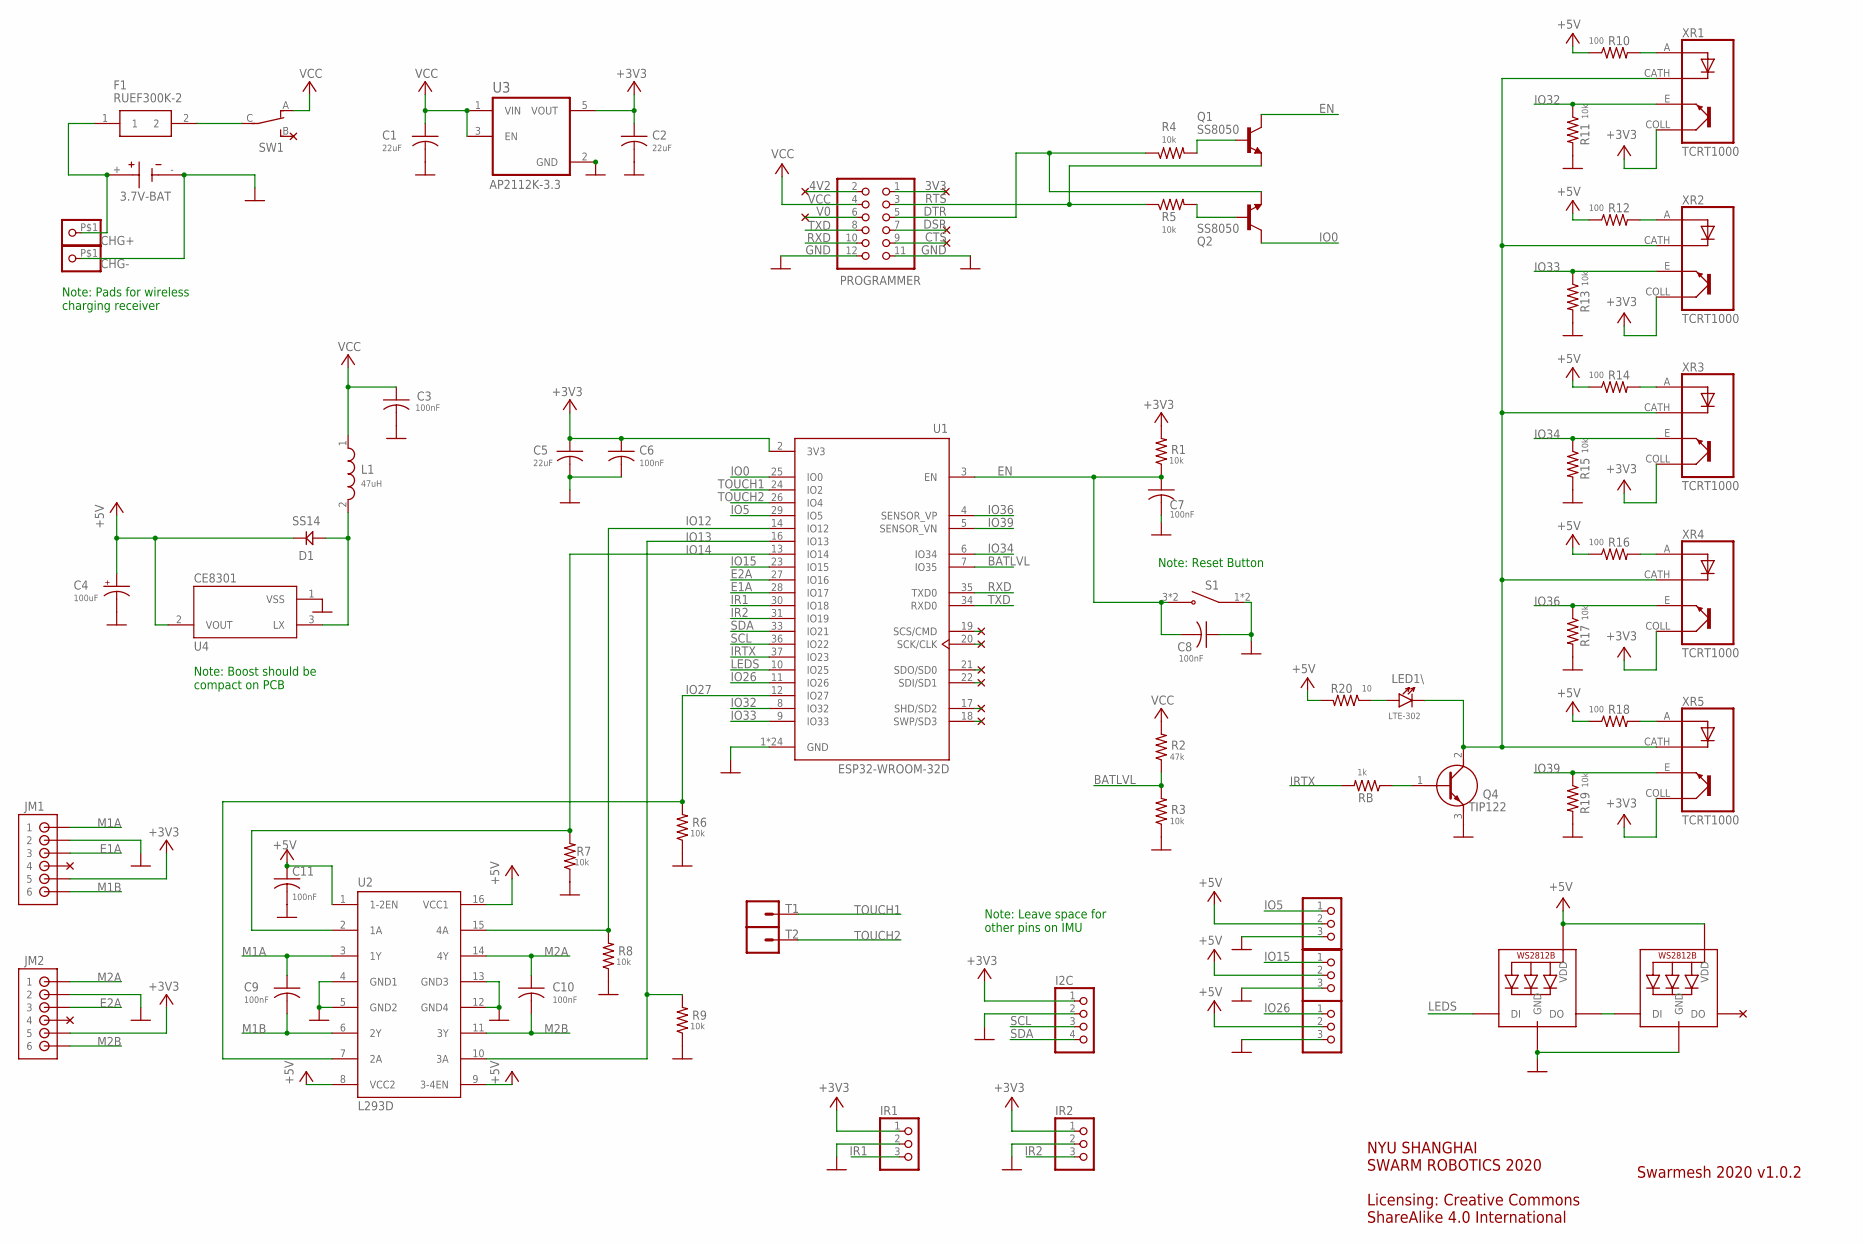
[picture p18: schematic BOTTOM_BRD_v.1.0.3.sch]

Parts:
BT: 3.7V-BAT; BAT_6S-AA
C1, C2, C5: 22uF; C0805
C3, C6, C7, C8, C9, C10, C11: 100nF; C0805
C4: 100uF; 153CLV-0605
CHARGING: WS2812B5050; WS2812B
CHG+: PINHD-1X1-BIGPOGO; 1X1-BIGPOGO
CHG-: PINHD-1X1-BIGPOGO; 1X1-BIGPOGO
D1: SS14; DO214
F1: RUEF300K-2; RUEF300K2
GPIO5, GPIO15, GPIO26: PINHD-1X3; 1X03
I2C: PINHD-1X4; 1X04
IR1, IR2: PINHD-1X3; 1X03
JM1, JM2: B6B-ZR
L1: 47uH; INDP5858X480N
LED1\: LTE-302
PROGRAMMER: PINHD-2X6; 2X06
Q1, Q2: SS8050; SOT23
Q4: TIP122; TO270P460X1020X2008-3P
R1, R3, R4, R5, R6, R7, R8, R9, R11, R13, R15, R17, R19: 10k; M0805
R2: 47k; M0805
R10, R12, R14, R16, R18: 100; M0805
R20: 10; M0805
RB: 1k; M0805
S1: 2-1437565-9; SW_2-1437565-9
STATE: WS2812B5050; WS2812B
SW1: CS12ANW03
T1, T2: CONN_01SPRING-CONN; SPRING-CONNECTOR
U1: ESP32-WROOM-32D; MODULE_ESP32-WROOM-32D
U2: L293D; DIL16
U3: AP2112K-3.3; SOT95P285X140-5N
U4: CE8301; REG_MCP1702T-3302E/MB
XR1, XR2, XR3, XR4, XR5: TCRT1000; XDCR_TCRT1000

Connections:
3V3: PROGRAMMER.1
4V2: PROGRAMMER.2
+3V3: C2.1, C5.1, C6.1, I2C.1, IR1.1, IR2.1, JM1.5, JM2.5, R1.2, U1.2 (3V3), U3.5 (VOUT), XR1.COLL (CO), XR2.COLL (CO), XR3.COLL (CO), XR4.COLL (CO), XR5.COLL (CO)
+5V: C4.+, C11.1, CHARGING.1-VDD (VDD), D1.CATHODE (KATHODE), GPIO5.2, GPIO15.2, GPIO26.2, R10.1, R12.1, R14.1, R16.1, R18.1, R20.2, STATE.1-VDD (VDD), U2.1 (1-2EN), U2.8 (VCC2), U2.9 (3-4EN), U2.16 (VCC1), U4.2 (VOUT)
BATLVL: R2.1, R3.2, U1.7 (IO35)
CTS: PROGRAMMER.9
DSR: PROGRAMMER.7
DTR: PROGRAMMER.5, Q2.2 (E), R4.1
E1A: JM1.3, U1.28 (IO17)
E2A: JM2.3, U1.27 (IO16)
EN: C7.1, C8.2, Q1.3 (C), R1.1, S1.3 (NO), S1.4 (NO), U1.3 (EN)
GND: BT.-, C1.2, C2.2, C3.2, C4.-, C5.2, C6.2, C7.2, C8.1, C11.2, CHARGING.3-GND (GND), CHG-.P$1, GPIO5.3, GPIO15.3, GPIO26.3, I2C.2, IR1.2, IR2.2, JM1.2, JM2.2, PROGRAMMER.11, PROGRAMMER.12, Q4.3 (E), R3.1, R6.1, R7.1, R8.1, R9.1, R11.2, R13.2, R15.2, R17.2, R19.2, S1.1 (COM), S1.2 (COM), STATE.3-GND (GND), U1.1 (GND), U1.15 (GND), U1.38 (GND), U1.39_1 (GND), U1.39_2 (GND), U1.39_3 (GND), U1.39_4 (GND), U1.39_5 (GND), U1.39_6 (GND), U1.39_7 (GND), U1.39_8 (GND), U1.39_9 (GND), U1.39_10 (GND), U1.39_11 (GND), U1.39_12 (GND), U1.39_13 (GND), U1.39_14 (GND), U1.39_15 (GND), U1.39_16 (GND), U1.39_17 (GND), U1.39_18 (GND), U1.39_19 (GND), U1.39_20 (GND), U1.39_21 (GND), U2.4 (GND1), U2.5 (GND2), U2.12 (GND4), U2.13 (GND3), U3.2 (GND), U4.1 (VSS)
IO0: Q2.3 (C), U1.25 (IO0)
IO5: GPIO5.1, U1.29 (IO5)
IO12: R8.2, U1.14 (IO12), U2.15 (4A)
IO13: R9.2, U1.16 (IO13), U2.10 (3A)
IO14: R7.2, U1.13 (IO14), U2.2 (1A)
IO15: GPIO15.1, U1.23 (IO15)
IO26: GPIO26.1, U1.11 (IO26)
IO27: R6.2, U1.12 (IO27), U2.7 (2A)
IO32: R11.1, U1.8 (IO32), XR1.E
IO33: R13.1, U1.9 (IO33), XR2.E
IO34: R15.1, U1.6 (IO34), XR3.E
IO36: R17.1, U1.4 (SENSOR_VP), XR4.E
IO39: R19.1, U1.5 (SENSOR_VN), XR5.E
IR1: IR1.3, U1.30 (IO18)
IR2: IR2.3, U1.31 (IO19)
IRTX: RB.2, U1.37 (IO23)
LEDS: CHARGING.4-DIN (DI), U1.10 (IO25)
M1A: C9.1, JM1.1, U2.3 (1Y)
M1B: C9.2, JM1.6, U2.6 (2Y)
M2A: C10.1, JM2.1, U2.14 (4Y)
M2B: C10.2, JM2.6, U2.11 (3Y)
unnamed: BT.+, CHG+.P$1, F1.1
unnamed: Q4.1 (B), RB.1
unnamed: F1.2, SW1.C
unnamed: D1.ANODE, L1.2, U4.3 (LX)
unnamed: R12.2, XR2.A
unnamed: R16.2, XR4.A
unnamed: LED1\.C, Q4.2 (C), XR1.CATH (C), XR2.CATH (C), XR3.CATH (C), XR4.CATH (C), XR5.CATH (C)
unnamed: CHARGING.2-DOUT (DO), STATE.4-DIN (DI)
unnamed: R14.2, XR3.A
unnamed: R18.2, XR5.A
unnamed: Q1.1 (B), R4.2
unnamed: R10.2, XR1.A
unnamed: LED1\.A, R20.1
unnamed: Q2.1 (B), R5.2
RTS: PROGRAMMER.3, Q1.2 (E), R5.1
RXD: PROGRAMMER.10, U1.35 (TXD0)
SCL: I2C.3, U1.36 (IO22)
SDA: I2C.4, U1.33 (IO21)
TOUCH1: T1.P$2, U1.24 (IO2)
TOUCH2: T2.P$2, U1.26 (IO4)
TXD: PROGRAMMER.8, U1.34 (RXD0)
V0: PROGRAMMER.6
VCC: C1.1, C3.1, L1.1, PROGRAMMER.4, R2.2, SW1.A, U3.1 (VIN), U3.3 (EN)

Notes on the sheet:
Note: Pads for wireless charging receiver
Note: Boost should be compact on PCB
Note: Leave space for other pins on IMU
Note: Reset Button
Swarmesh 2020 v1.0.2
NYU SHANGHAI SWARM ROBOTICS 2020 Licensing: Creative Commons ShareAlike 4.0 International

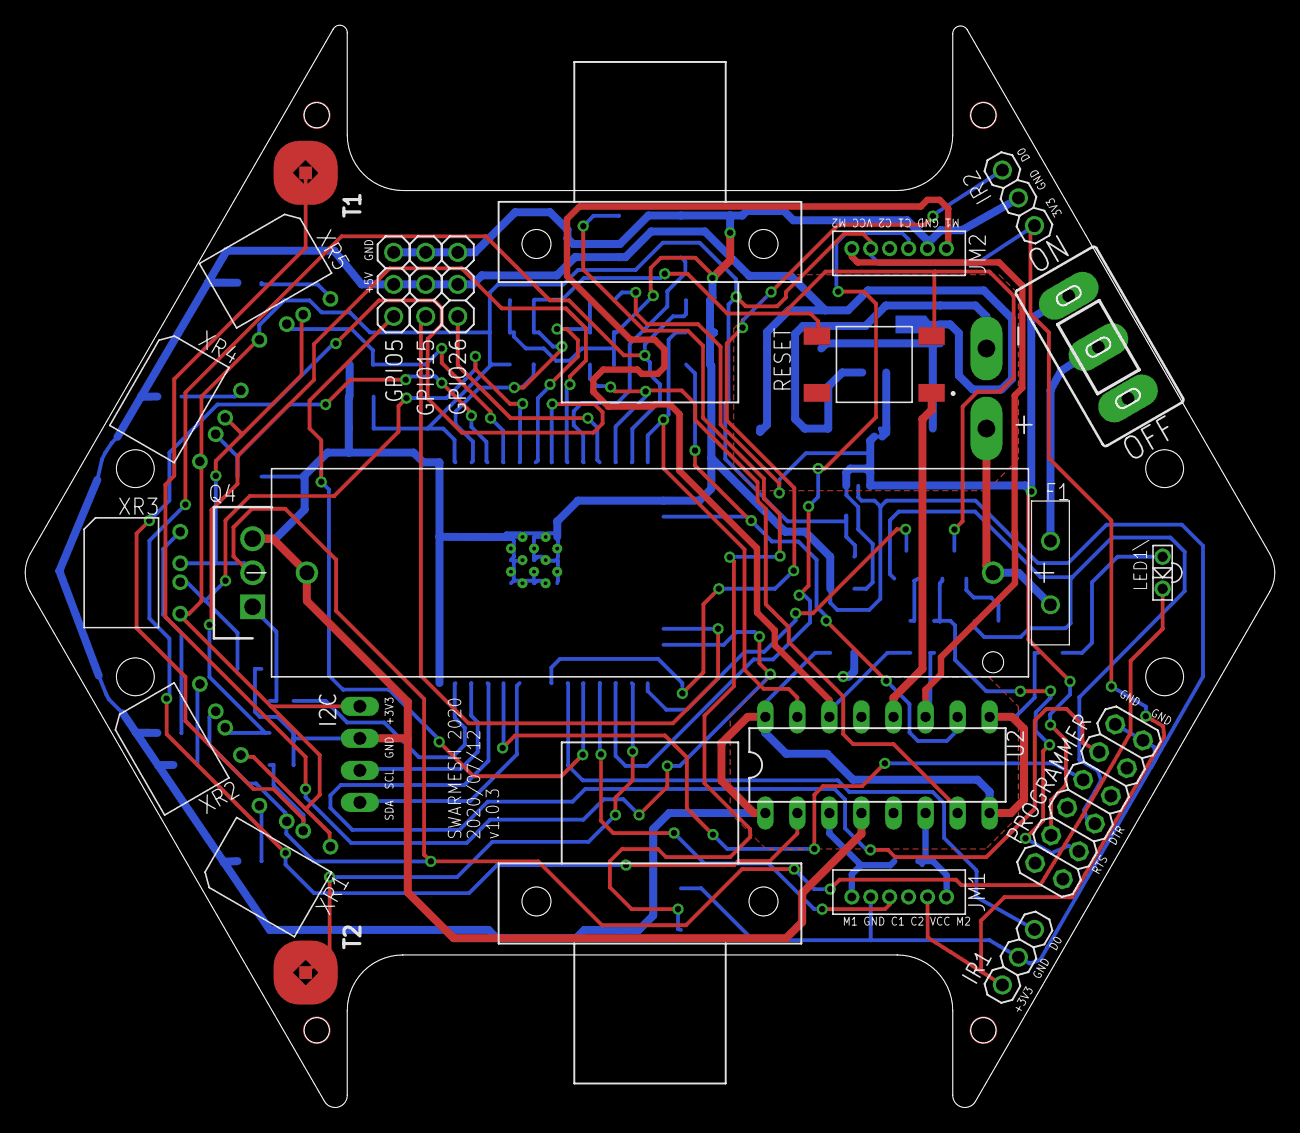
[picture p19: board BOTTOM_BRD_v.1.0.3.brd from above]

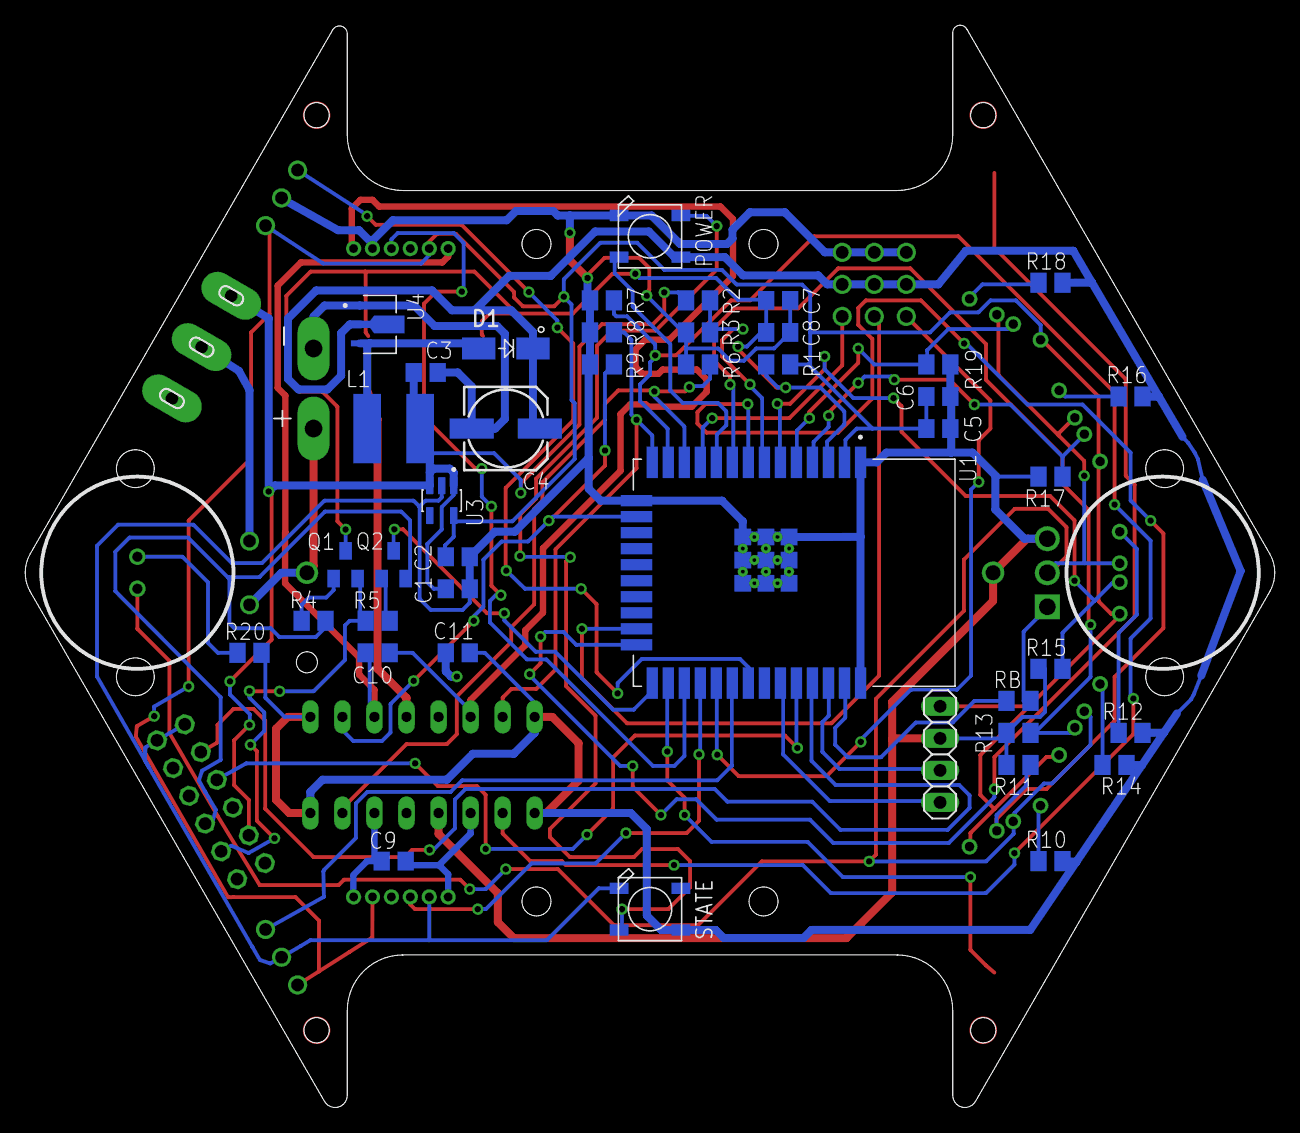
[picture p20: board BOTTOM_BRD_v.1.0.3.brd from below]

Board: 2 copper layers, 99.1 x 85.8 mm, 66 parts (43 on the bottom side), 51 nets.

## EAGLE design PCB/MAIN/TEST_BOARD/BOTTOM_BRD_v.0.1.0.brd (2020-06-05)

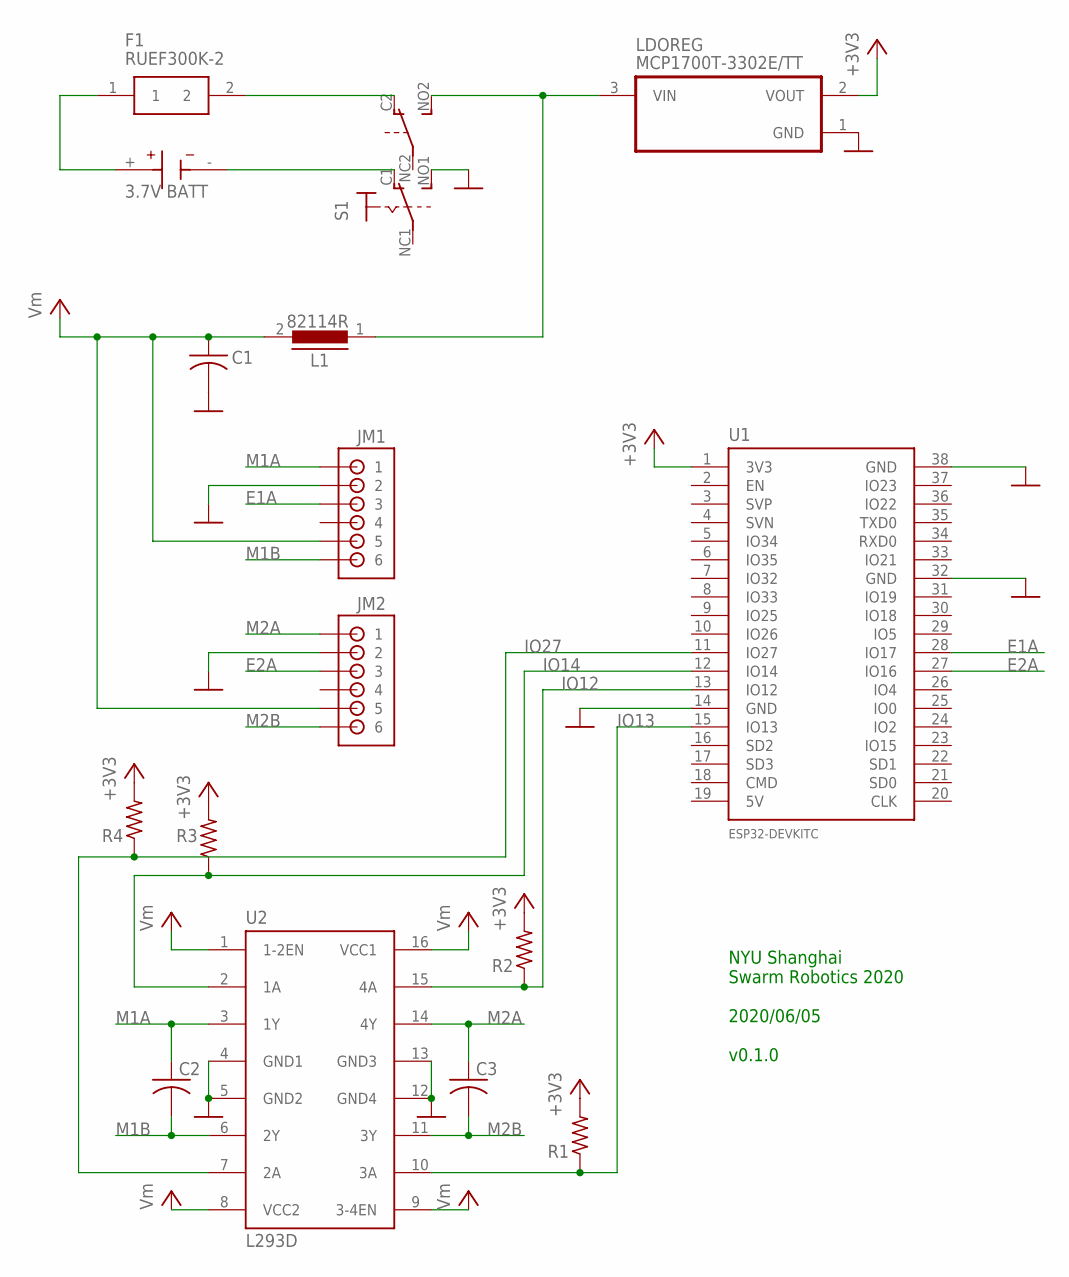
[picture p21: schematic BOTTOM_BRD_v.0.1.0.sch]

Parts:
BT1: 3.7V BATT; BAT_6S-AA
C1: C-US025-030X050; C025-030X050
C2, C3: C-US025-025X050; C025-025X050
F1: RUEF300K-2; RUEF300K2
JM1, JM2: B6B-ZR
L1: 82114R
LDOREG: MCP1700T-3302E/TT; SOT95P237X112-3N
R1, R2, R3, R4: R-US_0207/9; 0207/9
S1: SWITCH_320-938; PS22F03
U1: ESP32DEVKITC; ESP32-DEVKITC
U2: L293D; DIL16

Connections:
+3V3: LDOREG.2 (VOUT), R1.2, R2.2, R3.2, R4.2, U1.1 (3V3)
E1A: JM1.3, U1.28 (IO17)
E2A: JM2.3, U1.27 (IO16)
GND: C1.2, JM1.2, JM2.2, LDOREG.1 (GND), S1.NO1 (S), U1.14 (GND), U1.32 (GND), U1.38 (GND), U2.4 (GND1), U2.5 (GND2), U2.12 (GND4), U2.13 (GND3)
IO12: R2.1, U1.13 (IO12), U2.15 (4A)
IO13: R1.1, U1.15 (IO13), U2.10 (3A)
IO14: R3.1, U1.12 (IO14), U2.2 (1A)
IO27: R4.1, U1.11 (IO27), U2.7 (2A)
M1A: C2.1, JM1.1, U2.3 (1Y)
M1B: C2.2, JM1.6, U2.6 (2Y)
M2A: C3.1, JM2.1, U2.14 (4Y)
M2B: C3.2, JM2.6, U2.11 (3Y)
unnamed: BT1.+, F1.1
unnamed: F1.2, S1.C2 (O)
unnamed: BT1.-, S1.C1 (O)
unnamed: L1.1, LDOREG.3 (VIN), S1.NO2 (S)
VCC: C1.1, JM1.5, JM2.5, L1.2, U2.1 (1-2EN), U2.8 (VCC2), U2.9 (3-4EN), U2.16 (VCC1)

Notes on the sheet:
NYU Shanghai Swarm Robotics 2020 2020/06/05 v0.1.0

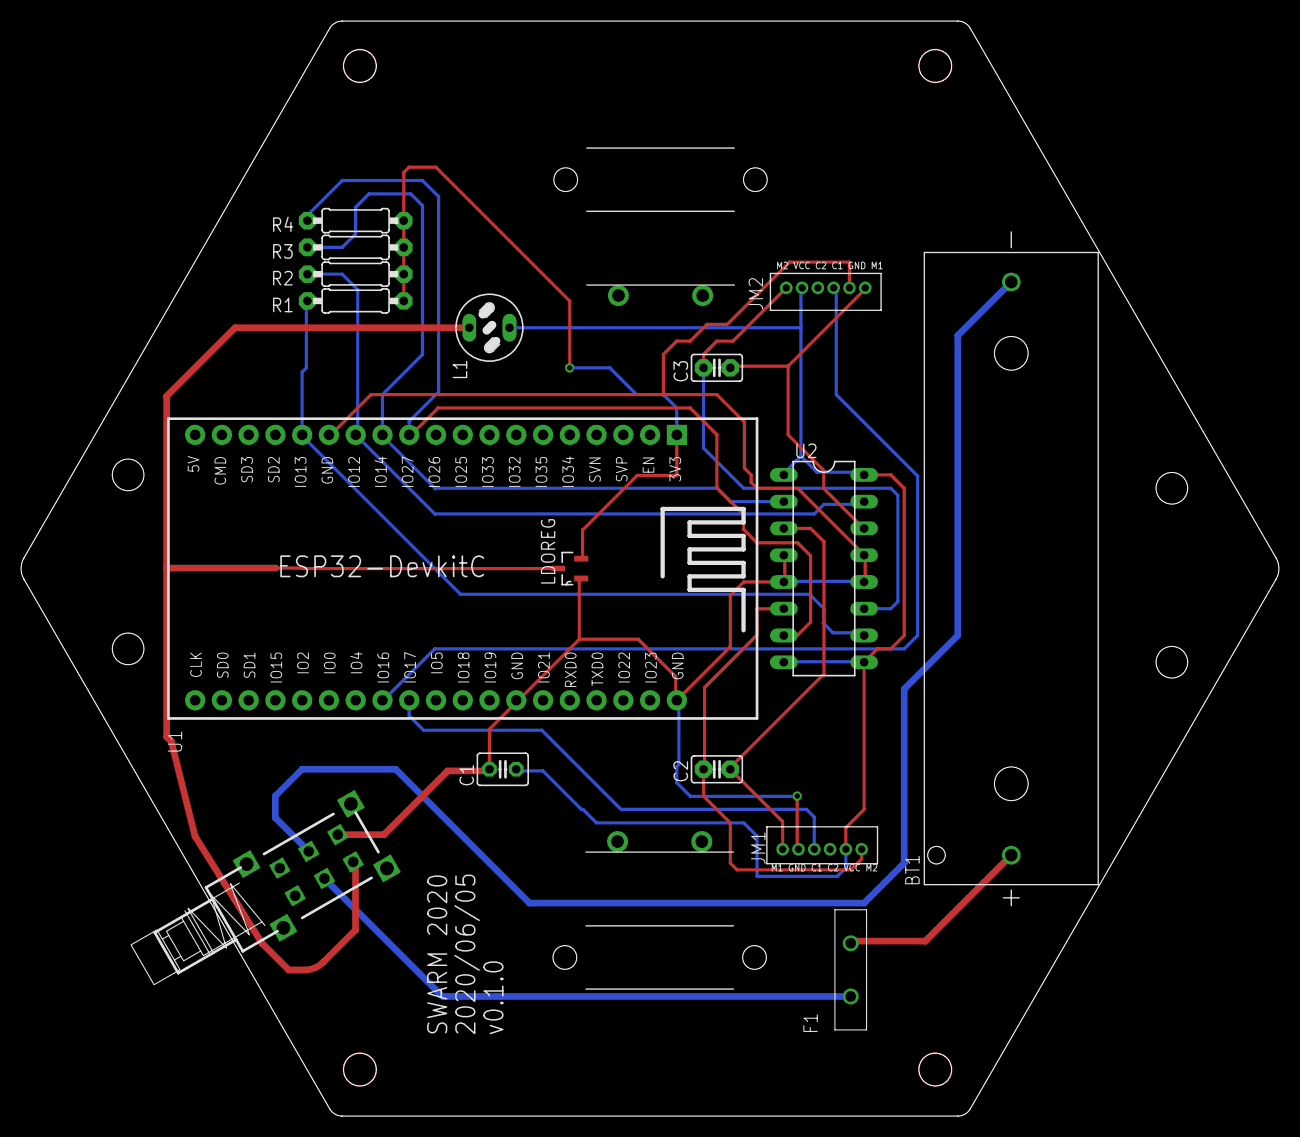
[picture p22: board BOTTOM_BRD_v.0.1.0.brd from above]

Board: 2 copper layers, 119.4 x 103.9 mm, 18 parts (0 on the bottom side), 17 nets.

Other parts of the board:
U$1, U$7: MOTOR10MM; VIBE-MOTOR-10MM

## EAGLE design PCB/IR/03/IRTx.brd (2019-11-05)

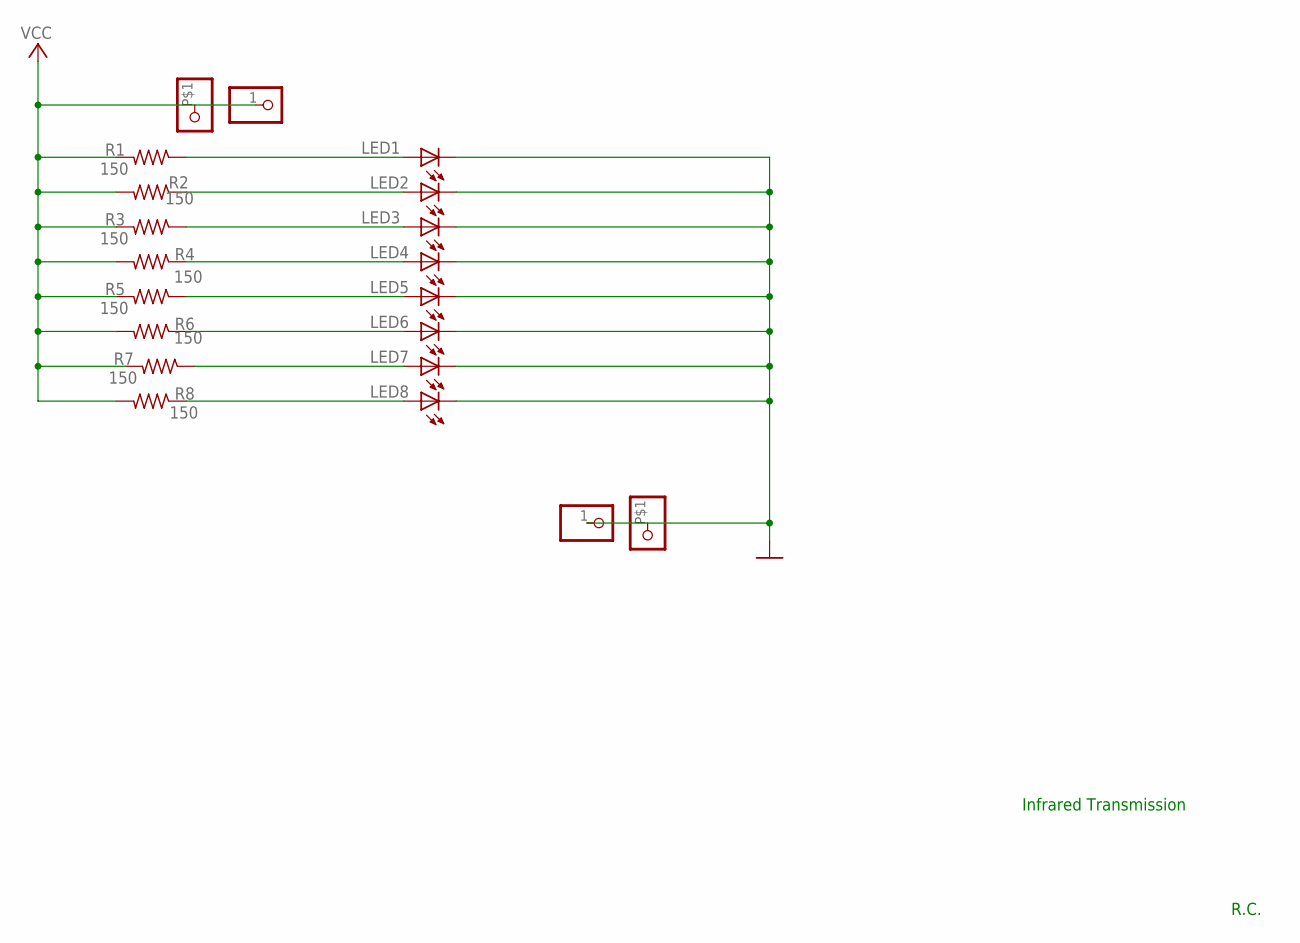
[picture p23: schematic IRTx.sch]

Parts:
JP1: 3.3; 1X1-BIGPOGO
JP2: GND; 1X1-BIGPOGO
JP3, JP4: PINHD-1X1; 1X01
LED1, LED2, LED3, LED4, LED5, LED6, LED7, LED8: LED5MM
R1, R2, R3, R4, R5, R6, R7, R8: 150; 0207/10

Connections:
GND: JP2.P$1, JP4.1, LED1.K (C), LED2.K (C), LED3.K (C), LED4.K (C), LED5.K (C), LED6.K (C), LED7.K (C), LED8.K (C)
unnamed: LED2.A, R2.1
unnamed: LED1.A, R1.1
unnamed: LED3.A, R3.1
unnamed: LED4.A, R4.1
unnamed: LED5.A, R5.1
unnamed: LED6.A, R6.1
unnamed: LED7.A, R7.1
unnamed: LED8.A, R8.1
VCC: JP1.P$1, JP3.1, R1.2, R2.2, R3.2, R4.2, R5.2, R6.2, R7.2, R8.2

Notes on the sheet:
Infrared Transmission
R.C.

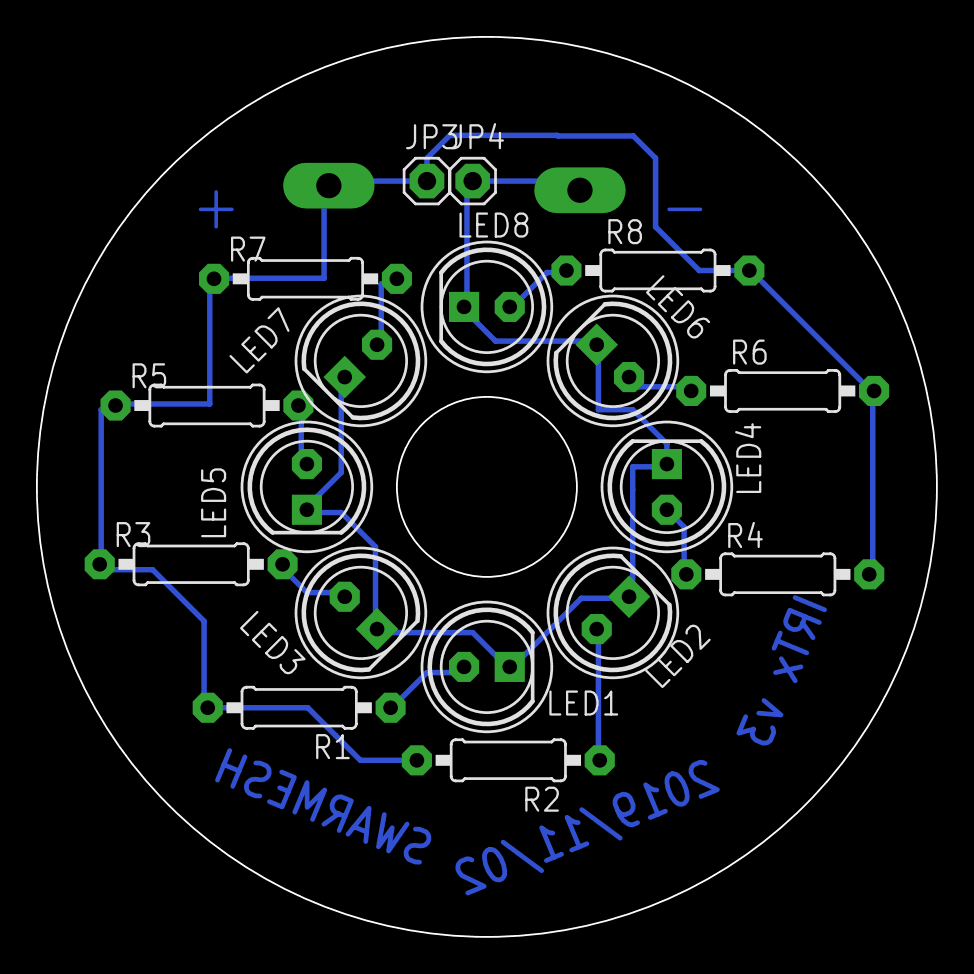
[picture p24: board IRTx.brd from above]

Board: 2 copper layers, 50.0 x 50.0 mm, 20 parts (0 on the bottom side), 10 nets.

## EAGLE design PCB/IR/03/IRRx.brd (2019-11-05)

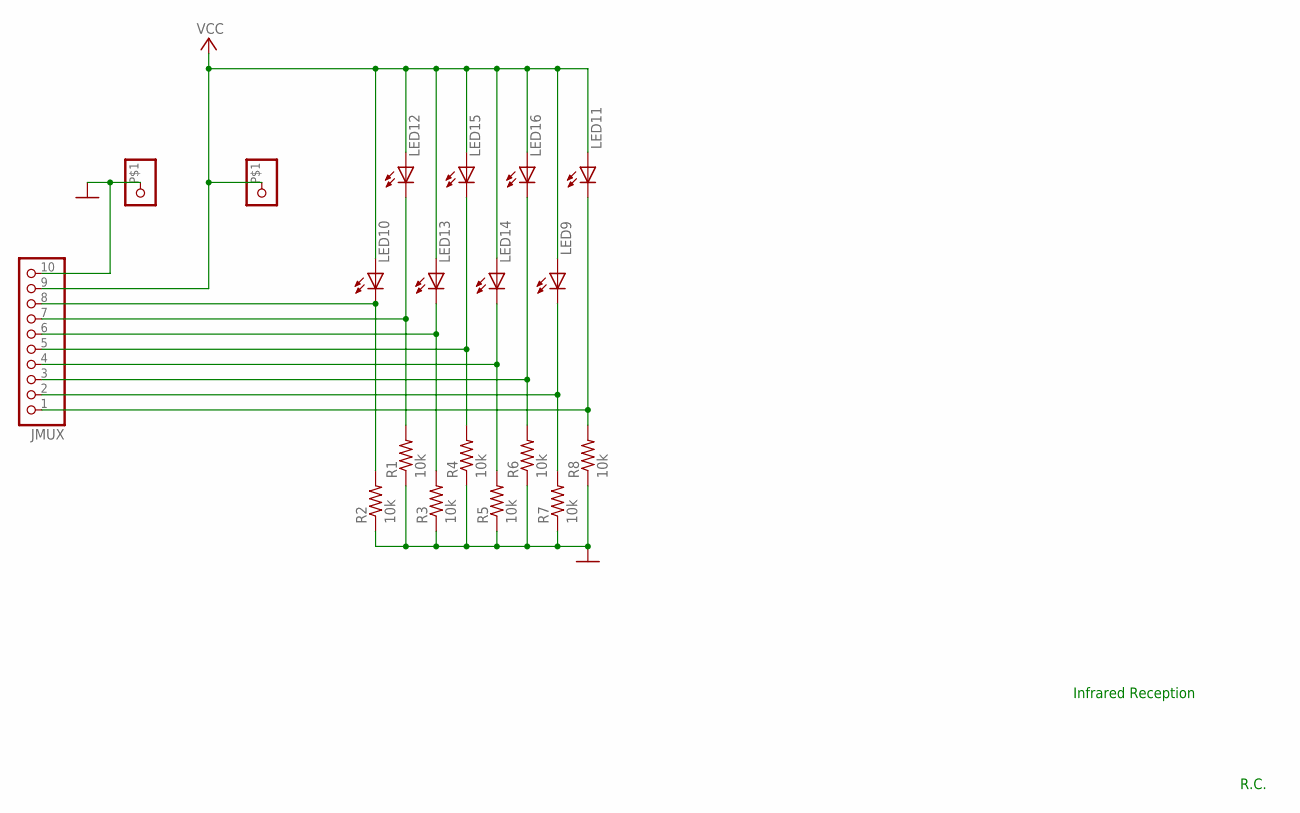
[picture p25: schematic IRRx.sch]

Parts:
JMUX: PINHD-1X10; 1X10-BIG
JP1: 3.3; 1X1-BIGPOGO
JP2: GND; 1X1-BIGPOGO
LED9, LED10, LED11, LED12, LED13, LED14, LED15, LED16: LED5MM
R1, R2, R3, R4, R5, R6, R7, R8: 10k; 0207/10

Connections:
GND: JMUX.10, JP2.P$1, R1.1, R2.1, R3.1, R4.1, R5.1, R6.1, R7.1, R8.1
unnamed: JMUX.8, LED10.K (C), R2.2
unnamed: JMUX.7, LED12.K (C), R1.2
unnamed: JMUX.6, LED13.K (C), R3.2
unnamed: JMUX.5, LED15.K (C), R4.2
unnamed: JMUX.4, LED14.K (C), R5.2
unnamed: JMUX.3, LED16.K (C), R6.2
unnamed: JMUX.2, LED9.K (C), R7.2
unnamed: JMUX.1, LED11.K (C), R8.2
VCC: JMUX.9, JP1.P$1, LED9.A, LED10.A, LED11.A, LED12.A, LED13.A, LED14.A, LED15.A, LED16.A

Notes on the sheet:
Infrared Reception
R.C.

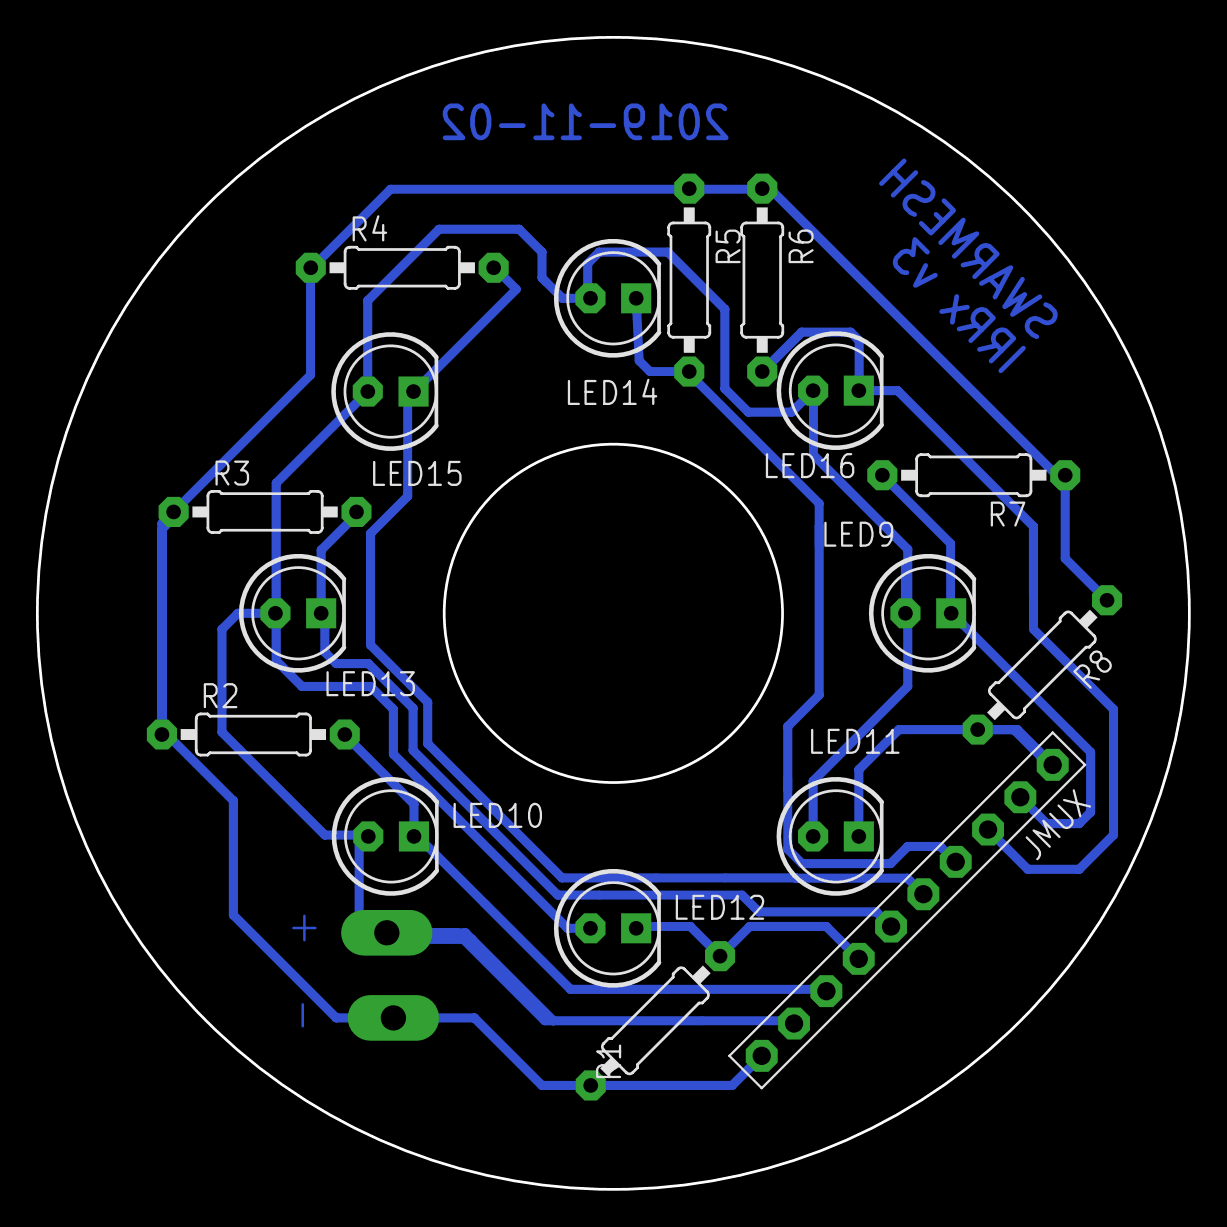
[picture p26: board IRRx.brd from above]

Board: 2 copper layers, 64.0 x 64.0 mm, 19 parts (0 on the bottom side), 10 nets.

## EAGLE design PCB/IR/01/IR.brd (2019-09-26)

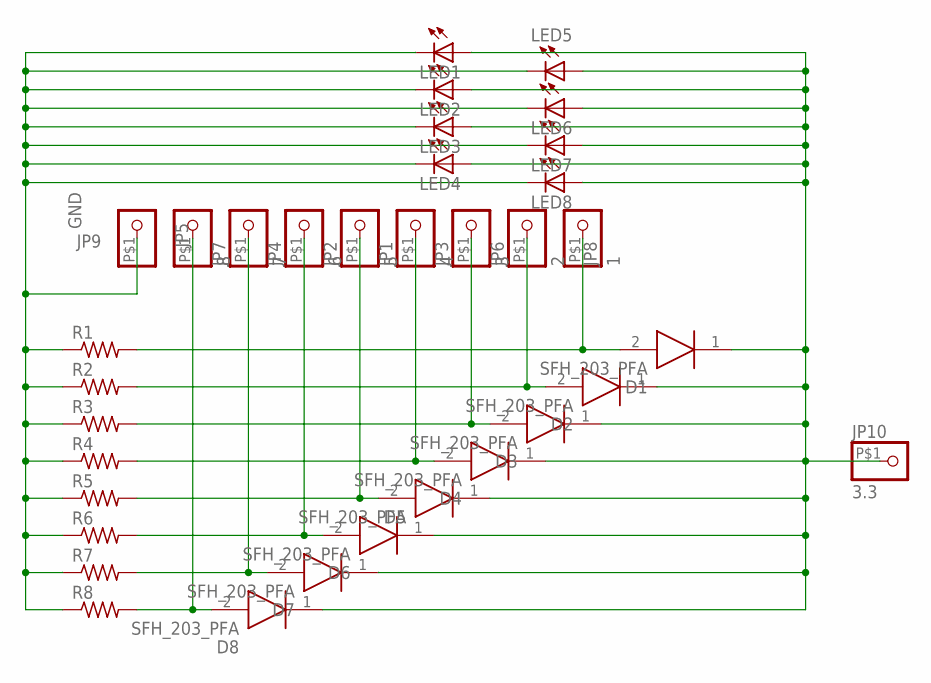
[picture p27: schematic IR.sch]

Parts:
D1, D2, D3, D4, D5, D6, D7, D8: SFH_203_PFA; SFH213_1
JP1: 4; 1X1-BIGPOGO
JP2: 5; 1X1-BIGPOGO
JP3: 3; 1X1-BIGPOGO
JP4: 6; 1X1-BIGPOGO
JP5: 8; 1X1-BIGPOGO
JP6: 2; 1X1-BIGPOGO
JP7: 7; 1X1-BIGPOGO
JP8: 1; 1X1-BIGPOGO
JP9: GND; 1X1-BIGPOGO
JP10: 3.3; 1X1-BIGPOGO
LED1, LED2, LED3, LED4, LED5, LED6, LED7, LED8: LED5MM
R1, R2, R3, R4, R5, R6, R7, R8: R-US_0207/10; 0207/10

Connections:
unnamed: D1.2 (A), JP8.P$1, R1.2
unnamed: D2.2 (A), JP6.P$1, R2.2
unnamed: D3.2 (A), JP3.P$1, R3.2
unnamed: D4.2 (A), JP1.P$1, R4.2
unnamed: D5.2 (A), JP2.P$1, R5.2
unnamed: D6.2 (A), JP4.P$1, R6.2
unnamed: D7.2 (A), JP7.P$1, R7.2
unnamed: D8.2 (A), JP5.P$1, R8.2
unnamed: D1.1 (K), D2.1 (K), D3.1 (K), D4.1 (K), D5.1 (K), D6.1 (K), D7.1 (K), D8.1 (K), JP10.P$1, LED1.A, LED2.A, LED3.A, LED4.A, LED5.A, LED6.A, LED7.A, LED8.A
unnamed: JP9.P$1, LED1.K (C), LED2.K (C), LED3.K (C), LED4.K (C), LED5.K (C), LED6.K (C), LED7.K (C), LED8.K (C), R1.1, R2.1, R3.1, R4.1, R5.1, R6.1, R7.1, R8.1

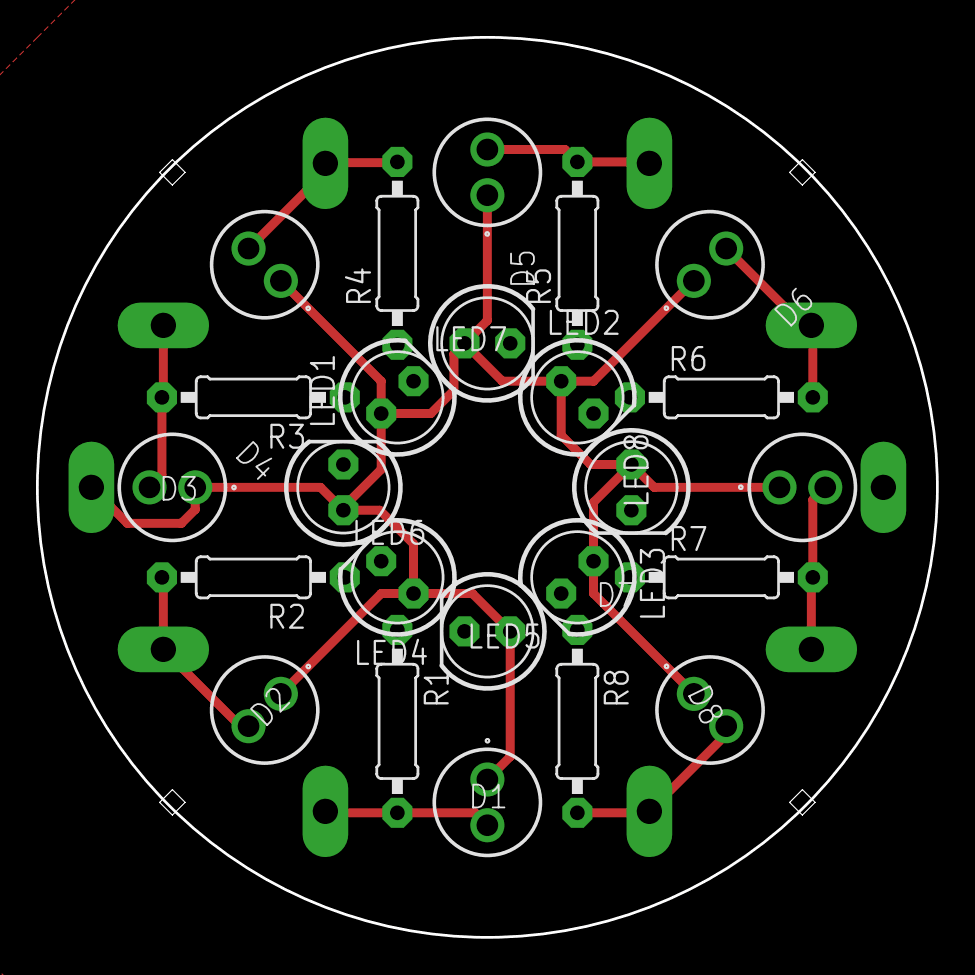
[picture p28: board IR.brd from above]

Board: 2 copper layers, 50.0 x 50.0 mm, 34 parts (0 on the bottom side), 10 nets.

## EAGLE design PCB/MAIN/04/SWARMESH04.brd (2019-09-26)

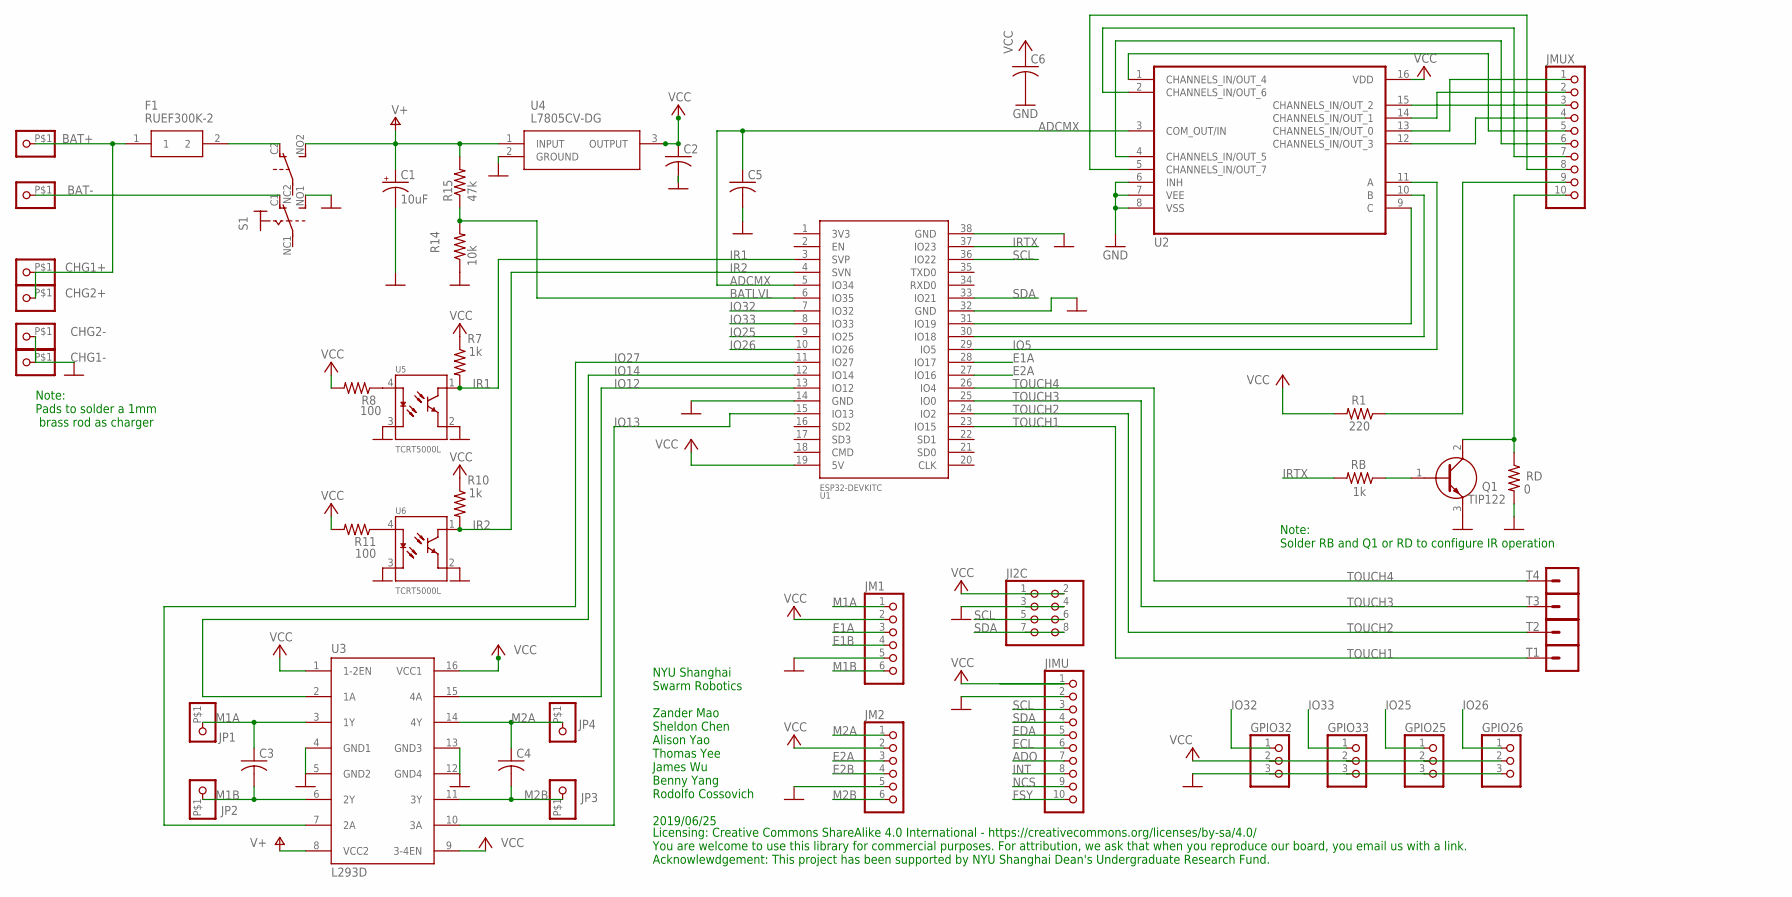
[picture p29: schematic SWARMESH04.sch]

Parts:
BAT+: PINHD-1X1-BIGPOGO; 1X1-BIGPOGO
BAT-: PINHD-1X1-BIGPOGO; 1X1-BIGPOGO
C1: 10uF; E2-5
C2, C5: C-US025-030X050; C025-030X050
C3, C4, C6: C-US025-025X050; C025-025X050
CHG1+, CHG1-, CHG2+, CHG2-: PINHD-1X1-BIGPOGO; 1X1-BIGPOGO
F1: RUEF300K-2; RUEF300K2
GPIO25, GPIO26, GPIO32, GPIO33: PINHD-1X3; 1X03
JI2C: PINHD-2X4; 2X04
JIMU: PINHD-1X10; 1X10-BIG
JM1, JM2: PINHD-1X6; 1X06
JMUX: PINHD-1X10; 1X10-BIG
JP1, JP2, JP3, JP4: PINHD-1X1-BIGPOGO; 1X1-BIGPOGO
Q1: TIP122; TO270P460X1020X2008-3P
R1: 220; 0207/9
R7, R10: 1k; 0207/9
R8, R11: 100; 0207/9
R14: 10k; 0207/9
R15: 47k; 0207/9
RB: 1k; 0207/9
RD: 0; 0207/9
S1: SWITCH_320-938; PS22F03
T1, T2, T3, T4: CONN_01SPRING-CONN; SPRING-CONNECTOR
U1: ESP32DEVKITC; ESP32-DEVKITC
U2: CD4051BEE4; CD4051BEE4DIP
U3: L293D; DIL16
U4: L7805CV-DG; TO270P460X1020X2008-3P
U5, U6: TCRT5000L; XDCR_TCRT5000L

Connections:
ADCMX: C5.1, U1.5 (IO34), U2.3 (COM_OUT/IN)
ADO: JIMU.7
BATLVL: R14.2, R15.1, U1.6 (IO35)
E1A: JM1.3, U1.28 (IO17)
E1B: JM1.4
E2A: JM2.3, U1.27 (IO16)
E2B: JM2.4
ECL: JIMU.6
EDA: JIMU.5
FSY: JIMU.10
GND: C1.-, C2.2, C5.2, C6.2, CHG1-.P$1, CHG2-.P$1, GPIO25.3, GPIO26.3, GPIO32.3, GPIO33.3, JI2C.3, JI2C.4, JIMU.2, JM1.5, JM2.5, Q1.3 (E), R14.1, RD.2, S1.NO1 (S), U1.14 (GND), U1.32 (GND), U1.38 (GND), U2.6 (INH), U2.7 (VEE), U2.8 (VSS), U3.4 (GND1), U3.5 (GND2), U3.12 (GND4), U3.13 (GND3), U4.2 (GROUND), U5.2 (E), U5.3 (C), U6.2 (E), U6.3 (C)
INT: JIMU.8
IO5: U1.29 (IO5), U2.11 (A)
IO12: U1.13 (IO12), U3.15 (4A)
IO13: U1.15 (IO13), U3.10 (3A)
IO14: U1.12 (IO14), U3.2 (1A)
IO25: GPIO25.1, U1.9 (IO25)
IO26: GPIO26.1, U1.10 (IO26)
IO27: U1.11 (IO27), U3.7 (2A)
IO32: GPIO32.1, U1.7 (IO32)
IO33: GPIO33.1, U1.8 (IO33)
IR1: R7.2, U1.3 (SVP), U5.1 (CO)
IR2: R10.2, U1.4 (SVN), U6.1 (CO)
IRTX: RB.2, U1.37 (IO23)
M1A: C3.1, JM1.1, JP1.P$1, U3.3 (1Y)
M1B: C3.2, JM1.6, JP2.P$1, U3.6 (2Y)
M2A: C4.1, JM2.1, JP4.P$1, U3.14 (4Y)
M2B: C4.2, JM2.6, JP3.P$1, U3.11 (3Y)
unnamed: Q1.1 (B), RB.1
unnamed: F1.2, S1.C2 (O)
unnamed: BAT-.P$1, S1.C1 (O)
unnamed: JMUX.6, U2.4 (CHANNELS_IN/OUT_5)
unnamed: U1.30 (IO18), U2.10 (B)
unnamed: U1.31 (IO19), U2.9 (C)
unnamed: R11.1, U6.4 (A)
unnamed: R8.1, U5.4 (A)
unnamed: JMUX.5, U2.1 (CHANNELS_IN/OUT_4)
unnamed: JMUX.7, U2.2 (CHANNELS_IN/OUT_6)
unnamed: JMUX.8, U2.5 (CHANNELS_IN/OUT_7)
unnamed: BAT+.P$1, CHG1+.P$1, CHG2+.P$1, F1.1
unnamed: JMUX.9, R1.1
unnamed: JMUX.10, Q1.2 (C), RD.1
unnamed: JMUX.1, U2.13 (CHANNELS_IN/OUT_0)
unnamed: JMUX.2, U2.14 (CHANNELS_IN/OUT_1)
unnamed: JMUX.4, U2.12 (CHANNELS_IN/OUT_3)
unnamed: JMUX.3, U2.15 (CHANNELS_IN/OUT_2)
NCS: JIMU.9
SCL: JI2C.5, JI2C.6, JIMU.3, U1.36 (IO22)
SDA: JI2C.7, JI2C.8, JIMU.4, U1.33 (IO21)
TOUCH1: T1.P$2, U1.23 (IO15)
TOUCH2: T2.P$2, U1.24 (IO2)
TOUCH3: T3.P$2, U1.25 (IO0)
TOUCH4: T4.P$2, U1.26 (IO4)
V+: C1.+, R15.2, S1.NO2 (S), U3.8 (VCC2), U4.1 (INPUT)
VCC: C2.1, C6.1, GPIO25.2, GPIO26.2, GPIO32.2, GPIO33.2, JI2C.1, JI2C.2, JIMU.1, JM1.2, JM2.2, R1.2, R7.1, R8.2, R10.1, R11.2, U1.19 (5V), U2.16 (VDD), U3.1 (1-2EN), U3.9 (3-4EN), U3.16 (VCC1), U4.3 (OUTPUT)

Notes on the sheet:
NYU Shanghai Swarm Robotics Zander Mao Sheldon Chen Alison Yao Thomas Yee James Wu Benny Yang Rodolfo Cossovich 2019/06/25
Licensing: Creative Commons ShareAlike 4.0 International - https://creativecommons.org/licenses/by-sa/4.0/ You are welcome to use this library for commercial purposes. For attribution, we ask that when you reproduce our board, you email us with a link. Acknowlewdgement: This project has been suppor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
Note: Solder RB and Q1 or RD to configure IR operation
Note: Pads to solder a 1mm brass rod as charger

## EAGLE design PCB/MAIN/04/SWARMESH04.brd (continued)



Board: 2 copper layers, 75.0 x 75.0 mm, 47 parts (7 on the bottom side), 47 nets.

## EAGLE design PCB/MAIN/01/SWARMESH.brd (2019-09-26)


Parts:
BAT+: PINHD-1X1-BIGPOGO; 1X1-BIGPOGO
BAT-: PINHD-1X1-BIGPOGO; 1X1-BIGPOGO
C1, C2, C3: 0.1uF; C050-024X044
C5, C6: 10uF; E2,5-7
CHG1+, CHG1-, CHG2+, CHG2-: PINHD-1X1-BIGPOGO; 1X1-BIGPOGO
GPIO17, GPIO25, GPIO26, GPIO32, GPIO33: PINHD-1X3; 1X03
IC1: 4051N; DIL16
IR1, IR2: CNY70; 4
JI2C: PINHD-2X4; 2X04
JIMU: PINHD-1X10; 1X10-BIG
JM1, JM2: PINHD-1X6; 1X06
JMUX: PINHD-1X10; 1X10-BIG
M1, M2: MOTOR10MM; VIBE-MOTOR-10MM
Q1: TIP122; TO220
R7, R10, R13: 1k; 0207/12
R8, R11: 100; 0207/12
R14: 10k; 0207/12
R15: 47k; 0207/12
RD1, RD2: 0; 0207/12
RS1, RS2: 150; 0207/12
S2: SWITCH_320-938; PS22F03
T1, T2, T3, T4: CONN_01SPRING-CONN; SPRING-CONNECTOR
U1: ESP32DEVKITC; ESP32-DEVKITC
U3: L293D; DIL16
U4: 7805T; TO220H

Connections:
ADCMX: C3.1, IC1.3 (X), U1.5 (IO34)
ADO: JIMU.7
BATLVL: R14.2, R15.1, U1.6 (IO35)
E1A: GPIO17.1, JM1.3, U1.28 (IO17)
E1B: JM1.4
E2A: JM2.3, U1.27 (IO16)
E2B: JM2.4
ECL: JIMU.6
EDA: JIMU.5
FSY: JIMU.10
GND: BAT-.P$1, C1.2, C2.2, C3.2, C5.-, C6.-, CHG1-.P$1, CHG2-.P$1, GPIO17.3, GPIO25.3, GPIO26.3, GPIO32.3, GPIO33.3, IC1.6 (INH), IC1.7 (VEE), IC1.8 (GND), IR1.E (EMI), IR1.K (C), IR2.E (EMI), IR2.K (C), JI2C.3, JI2C.4, JIMU.2, JM1.5, JM2.5, Q1.3 (E), R14.1, RD2.2, U1.14 (GND), U1.32 (GND), U1.38 (GND), U3.4 (GND1), U3.5 (GND2), U3.12 (GND4), U3.13 (GND3), U4.2 (GND)
INT: JIMU.8
IO5: IC1.11 (A), U1.11 (IO27), U1.12 (IO14), U1.13 (IO12), U1.15 (IO13), U1.29 (IO5), U3.2 (1A), U3.7 (2A), U3.10 (3A), U3.15 (4A)
IO18: IC1.10 (B), U1.30 (IO18)
IO19: IC1.9 (C), U1.31 (IO19)
IO25: GPIO25.1, U1.9 (IO25)
IO26: GPIO26.1, U1.10 (IO26)
IO32: GPIO32.1, U1.7 (IO32)
IO33: GPIO33.1, U1.8 (IO33)
IR1: IR1.C (COL), R7.2, U1.3 (SVP)
IR2: IR2.C (COL), R10.2, U1.4 (SVN)
IRTX: R13.2, U1.37 (IO23)
M1A: JM1.1, M1.+, U3.3 (1Y)
M1B: JM1.6, M1.-, U3.6 (2Y)
M2A: JM2.1, M2.-, U3.14 (4Y)
M2B: JM2.6, M2.+, U3.11 (3Y)
unnamed: Q1.1 (B), R13.1
unnamed: IC1.13 (X0), JMUX.1
unnamed: IC1.14 (X1), JMUX.2
unnamed: IC1.15 (X2), JMUX.3
unnamed: IC1.12 (X3), JMUX.4
unnamed: IC1.1 (X4), JMUX.5
unnamed: IC1.5 (X5), JMUX.6
unnamed: IC1.2 (X6), JMUX.7
unnamed: IC1.4 (X7), JMUX.8
unnamed: C6.+, JMUX.9, RS1.1, RS2.1
unnamed: JMUX.10, RD1.2, RD2.1
unnamed: IR2.A, R11.1
unnamed: BAT+.P$1, S2.NC1
unnamed: IR1.A, R8.1
unnamed: Q1.2 (C), RD1.1
NCS: JIMU.9
SCL: JI2C.5, JI2C.6, JIMU.3, U1.36 (IO22)
SDA: JI2C.7, JI2C.8, JIMU.4, U1.33 (IO21)
TOUCH1: T1.P$2, U1.23 (IO15)
TOUCH2: T2.P$2, U1.24 (IO2)
TOUCH3: T3.P$2, U1.25 (IO0)
TOUCH4: T4.P$2, U1.26 (IO4)
V+: C5.+, CHG1+.P$1, CHG2+.P$1, RS2.2, S2.NO1 (S), U3.8 (VCC2), U4.1 (VI)
VCC: C1.1, C2.1, GPIO17.2, GPIO25.2, GPIO26.2, GPIO32.2, GPIO33.2, IC1.16 (VCC), JI2C.1, JI2C.2, JIMU.1, JM1.2, JM2.2, R7.1, R8.2, R10.1, R11.2, RS1.2, U1.19 (5V), U3.1 (1-2EN), U3.9 (3-4EN), U3.16 (VCC1), U4.3 (VO)

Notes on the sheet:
Swarm Robotics
NYU Shanghai
2019/06/18
Zander Mao Sheldon Chen Allison Yao Thomas Yee James Wu Benny Yang Rodolfo Cossovich
Remember to change transistor footprint
Licensing: Creative Commons ShareAlike 4.0 International - https://creativecommons.org/licenses/by-sa/4.0/ You are welcome to use this library for commercial purposes. For attribution, we ask that when you reproduce our board, you email us with a link. Acknowlewdgement: This project has been suppor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
Remember to review CD4051 footprint & connections
Note: Select RS & RD to configure IR operation
check CNY70 footprint
Note: Pads to solder a 1mm brass rod as charger
Note: Touch Sensors could be connected to other sensors

Board: 2 copper layers, 46 parts (0 on the bottom side), 42 nets, no tracks yet.

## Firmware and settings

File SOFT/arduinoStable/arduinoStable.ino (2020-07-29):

////////////////////////////////////////////////////////////////////////////////////////////////////////////////////////////////////////////////////
/////////////////////////////////////THE ID OF THE ROBOT NEEDS TO BE SET ACCORDING TO THE ARUCO CODE IT CARRIES/////////////////////////////////////
////////////////////////////////////////////////////////////////////////////////////////////////////////////////////////////////////////////////////

#include <ArduinoJson.h>
#include "WiFi.h"
#include "AsyncUDP.h"

#define PWMA 27
#define DIRA 14
#define PWMB 12
#define DIRB 13
#define PULSE 7
//SET ACCORDING TO THE ARUCO CODE

int *POS;
int ORI;
int TURN;
int DIST;
int STATE = 0;
const char *ID;

class Destinations
{
private:
  int *_dst;
  int *_init_pos;
  int **_dst_lst;
  int _lst_size;
  void _del_dst_lst(int idx);

public:
  Destinations();
  void set_class();
  void select_dst(int *POS);
  void load_dst(DynamicJsonDocument &jTask, int *POS);
  void proceed_dst(DynamicJsonDocument &jDst, int *POS);
  int *get_dst();
  int arrive_dst(int *POS);
};

Destinations::Destinations()
{
  int **_dst_lst;
  int *_dst;
  int *_init_pos;
  int _lst_size;
}

void Destinations::set_class()
{
  _dst = (int *)malloc(sizeof(int) * 2);
  _init_pos = (int *)malloc(sizeof(int) * 2);
  for (int i = 0; i < 2; i++)
    _dst[i] = -1;
}

void Destinations::_del_dst_lst(int idx)
{
  //  _dst[0] = _dst_lst[idx][0];
  //  _dst[1] = _dst_lst[idx][1];
  // swap the value at index with the last element
  _dst_lst[idx][0] = _dst_lst[_lst_size - 1][0];
  _dst_lst[idx][1] = _dst_lst[_lst_size - 1][1];
  // modify _dst_lst and get rid of the smallest element
  _lst_size--;
  Serial.print("Reduced List Size: ");
  Serial.println(_lst_size);
  int **new_ptr = (int **)malloc(sizeof(int *) * (_lst_size));
  for (int i = 0; i < _lst_size; i++)
  {
    new_ptr[i] = (int *)malloc(sizeof(int) * 2);
    for (int j = 0; j < 2; j++)
    {
      new_ptr[i][j] = _dst_lst[i][j];
    }
    free(_dst_lst[i]);
  }
  free(_dst_lst);
  _dst_lst = new_ptr;
}

void Destinations::load_dst(DynamicJsonDocument &jTask, int *POS)
{
  for (int i = 0; i < 2; i++)
    _init_pos[i] = POS[i];
  _lst_size = jTask["Num"];
  Serial.print("Task size: ");
  Serial.println(_lst_size);
  _dst_lst = (int **)malloc(sizeof(int *) * _lst_size);
  // load json destination coordinates into the two-dimensional array
  for (int i = 0; i < _lst_size; i++)
  {
    _dst_lst[i] = (int *)malloc(sizeof(int) * 2);
    for (int j = 0; j < 2; j++)
    {
      _dst_lst[i][j] = jTask["Task"][i][j];
    }
  }
  // automatically acquire the next destination by calling the function
  select_dst(POS);
}

void Destinations::select_dst(int *POS)
{
  // select the destination with the least manhattan distance
  int x = _dst_lst[0][0];
  int y = _dst_lst[0][1];
  int idx = 0;
  int dist = (abs(x - POS[0]) + abs(y - POS[1]));
  for (int i = 0; i < _lst_size; i++)
  {
    x = _dst_lst[i][0];
    y = _dst_lst[i][1];
    int new_dist = (abs(x - POS[0]) + abs(y - POS[1]));
    if (new_dist < dist)
    {
      dist = new_dist;
      idx = i;
    }
  }
  for (int i = 0; i < 2; i++)
    _dst[i] = _dst_lst[idx][i];
  _del_dst_lst(idx);
}

void Destinations::proceed_dst(DynamicJsonDocument &jDst, int *POS)
{
  int *dst = (int *)malloc(sizeof(int) * 2);
  dst[0] = jDst["Pos"][0];
  dst[1] = jDst["Pos"][1];
  Serial.println(_lst_size);
  if (_lst_size > 0)
  {
    // proceed to the next least distance point
    if (dst[0] == _dst[0] && dst[1] == _dst[1])
    {
      select_dst(POS);
    }
    else
    {
      // get the id of the element
      int idx = -1;
      for (int i = 0; i < _lst_size; i++)
      {
        if (_dst_lst[i][0] == dst[0] && _dst_lst[i][1] == dst[1])
          idx = i;
        Serial.println("matched");
      }
      //      filter out destination of robots going back to their origin
      if (idx >= 0)
        _del_dst_lst(idx);
    }
  }
  else
  {
    // run out of available Destinations
    // go back to original point
    //    only doing so when the last destination conflicts the destination taken by others
    if (dst[0] == _dst[0] && dst[1] == _dst[1])
    {
      for (int i = 0; i < 2; i++)
        _dst[i] = _init_pos[i];
    }
  }
}

int *Destinations::get_dst()
{
  int *new_ptr = (int *)malloc(sizeof(int) * 2);
  for (int i = 0; i < 2; i++)
    new_ptr[i] = _dst[i];
  return new_ptr;
}

int Destinations::arrive_dst(int *POS)
{
  if (POS[0] == _dst[0] && POS[1] == _dst[1])
    return 1;
  return 0;
}

struct Tick
{
  const uint8_t PIN;
  uint32_t numberTicks;
  bool tickOn;
};

Tick encoder1 = {16, 0, false};
Tick encoder2 = {17, 0, false};

void IRAM_ATTR isr()
{
  encoder1.numberTicks += 1;
  encoder1.tickOn = true;
}

void IRAM_ATTR isr2()
{
  encoder2.numberTicks += 1;
  encoder2.tickOn = true;
}

const char *ssid = "nowifi";
const char *password = "durf2020";

AsyncUDP udp;
Destinations dstc;

void setup()
{
  //  SET UP THE ID OF THE ROBOT HERE
  ID = "7";
  pinMode(PWMB, OUTPUT);
  pinMode(DIRB, OUTPUT);
  pinMode(DIRA, OUTPUT);
  pinMode(PWMA, OUTPUT);
  Serial.begin(115200);
  WiFi.mode(WIFI_STA);
  WiFi.begin(ssid, password);
  pinMode(encoder1.PIN, INPUT_PULLUP);
  pinMode(encoder2.PIN, INPUT_PULLUP);
  attachInterrupt(encoder1.PIN, isr, FALLING);
  attachInterrupt(encoder2.PIN, isr2, FALLING);
  ledcAttachPin(PWMA, 1);
  ledcAttachPin(PWMB, 2);
  ledcSetup(1, 12000, 8);
  ledcSetup(2, 12000, 8);
  encoder1.numberTicks = 0;
  encoder2.numberTicks = 0;
  POS = (int *)malloc(sizeof(int) * 2);
  dstc.set_class();
  if (WiFi.waitForConnectResult() != WL_CONNECTED)
  {
    Serial.println("WiFi Failed");
    while (1)
    {
      delay(1000);
    }
  }
  //  listening to both task and current position on this channel
  if (udp.listenMulticast(IPAddress(224, 3, 29, 1), 10001))
  {
    udp.onPacket([](AsyncUDPPacket packet) {
      DynamicJsonDocument jInfo(1024);
      deserializeJson(jInfo, packet.data());
      const int Purpose = jInfo["Purpose"];
      switch (Purpose)
      {
      case 1:
      {
        Serial.println("Position received");

        //            not move if it can't get its position in json document
        if (!jInfo[ID][0][0] && !jInfo[ID][0][1])
          break;
        POS[0] = jInfo[ID][0][0];
        POS[1] = jInfo[ID][0][1];
        ORI = jInfo[ID][1];
        // move only if it has received tasks
        int *ptr = dstc.get_dst();
        int arrive = dstc.arrive_dst(POS);
        Serial.println(ptr[0]);
        Serial.println(ptr[1]);
        Serial.println();
        if (ptr[0] != -1 && !arrive)
        {
          actionDecoder(ORI, POS, ptr);
        }
        else if (arrive)
        {
          char jsonStr[80];
          //              jsonCreator(jsonStr);
          const size_t capacity = JSON_ARRAY_SIZE(2) + JSON_OBJECT_SIZE(2);
          DynamicJsonDocument doc(capacity);
          doc["Purpose"] = 3;
          JsonArray Pos = doc.createNestedArray("Pos");
          Pos.add(POS[0]);
          Pos.add(POS[1]);
          serializeJson(doc, jsonStr);
          doc.clear();
          udp.writeTo((const uint8_t *)jsonStr, strlen(jsonStr), IPAddress(224, 3, 29, 1), 10001);
        }
        free(ptr);
      }
      break;
      case 2:
        Serial.println("Tasks received");
        STATE = 1;
        dstc.load_dst(jInfo, POS);
        break;
      case 3:
        //        other robots have arrived at their destinations
        //        need to check whether the destinations are the same as its own destination
        //        move only when it self is not at the destination
        if (!dstc.arrive_dst(POS))
          dstc.proceed_dst(jInfo, POS);
      }
      jInfo.clear();
    });
  }
}

void loop()
{
  if (STATE == 1)
  {
    forward(1000);
  }
  else if (STATE == 2)
  {
    turnLeft(TURN);
  }
  else if (STATE == 3)
  {
    turnRight(TURN);
  }
}

//void dstSelector(int ORI, int *POS, int *DST, int *DST_LST, DynamicJsonDocument &jTask)
//{
//  //  const int* dst = jTask["Task"];
//  int x = jTask["Task"][0][0];
//  int y = jTask["Task"][0][1];
//  int idx = 0;
//  int dist = (abs(x - POS[0]) + abs(y - POS[1]));
//  const int len = jTask["Num"];
//  for (int i = 0; i < len; i++)
//  {
//    //  calc manhattan distance
//    int x = jTask["Task"][i][0];
//    int y = jTask["Task"][i][1];
//    int new_dist = (abs(x - POS[0]) + abs(y - POS[1]));
//    Serial.println(new_dist);
//    if (new_dist < dist)
//    {
//      dist = new_dist;
//      idx = i;
//    }
//  }
//  DST[0] = jTask["Task"][idx][0];
//  DST[1] = jTask["Task"][idx][1];
//}

//void jsonCreator(char* jsonStr) {
//  const size_t capacity = JSON_ARRAY_SIZE(2) + JSON_OBJECT_SIZE(2);
//  DynamicJsonDocument doc(capacity);
//  doc["Purpose"] = 3;
//  JsonArray Pos = doc.createNestedArray("Pos");
//  Pos.add(POS[0]);
//  Pos.add(POS[1]);
//  serializeJson(doc, jsonStr);
//  doc.clear();
//}

void actionDecoder(int ORI, int *POS, int *DST)
{
  //  calculate the robots' absolute position
  int x = DST[0] - POS[0];
  int y = DST[1] - POS[1];
  TURN = 90;
  if (abs(ORI) <= 5)
  {
    if (y >= 1)
    {
      STATE = 3;
      TURN = 180;
    }
    else if (y <= -1)
    {
      STATE = 1;
      DIST = y * 1000;
    }
    else
    {
      if (x >= 1)
      {
        STATE = 3;
      }
      else if (x <= -1)
      {
        STATE = 2;
      }
    }
  }
  else if (abs(ORI) >= 175)
  {
    if (y >= 1)
    {
      STATE = 1;
      DIST = abs(y) * 1000;
    }
    else if (y <= -1)
    {
      STATE = 3;
      TURN = 180;
    }
    else
    {
      if (x >= 1)
      {
        STATE = 2;
      }
      else if (x <= -1)
      {
        STATE = 3;
      }
    }
  }
  else if (ORI >= 85 && ORI <= 95)
  {
    if (x >= 1)
    {
      STATE = 1;
      DIST = x * 1000;
    }
    else if (x <= 1)
    {
      STATE = 3;
      TURN = 180;
    }
    else
    {
      if (y >= 1)
      {
        STATE = 2;
      }
      else if (y <= -1)
      {
        STATE = 3;
      }
    }
  }
  else if (ORI >= -95 && ORI <= -85)
  {
    if (x >= 1)
    {
      STATE = 3;
      TURN = 180;
    }
    else if (x <= -1)
    {
      STATE = 1;
      DIST = abs(x) * 1000;
    }
    else
    {
      if (y >= 1)
      {
        STATE = 3;
      }
      else if (y <= -1)
      {
        STATE = 2;
      }
    }
  }
  else
  {
    int remain = ORI % 90;
    if (abs(remain) >= 45)
    {
      STATE = (remain < 0) ? 2 : 3;
      TURN = 90 - abs(remain);
    }
    else
    {
      STATE = (remain > 0) ? 2 : 3;
      TURN = abs(remain);
    }
  }
}

void forward(int dist)
{
  if (encoder1.numberTicks < dist)
  {
    if (encoder1.numberTicks > encoder2.numberTicks)
    {
      motorA(200, 0);
      motorB(0, 0);
    }
    else if (encoder1.numberTicks < encoder2.numberTicks)
    {
      motorA(0, 0);
      motorB(200, 0);
    }
    else
    {
      motorA(200, 0);
      motorB(200, 0);
    }
  }
  else
  {
    motorA(0, 0);
    motorB(0, 0);
    encoder1.numberTicks = 0;
    encoder2.numberTicks = 0;
    STATE = 0;
  }
}

void turnLeft(int deg)
{
  if (encoder1.numberTicks <= PULSE * deg)
  {
    //    if ( encoder1.numberTicks > encoder2.numberTicks) {
    //      motorA (100, 0);
    //      motorB (0, 0);
    //    } else if ( encoder1.numberTicks < encoder2.numberTicks) {
    //      motorA (0, 0);
    //      motorB (100, 1);
    //    } else {
    motorA(100, 0);
    motorB(100, 1);
    //    }
  }
  else
  {
    motorA(0, 0);
    motorB(0, 0);
    encoder1.numberTicks = 0;
    encoder2.numberTicks = 0;
    STATE = 0;
  }
}

void turnRight(int deg)
{
  if (encoder1.numberTicks <= PULSE * deg)
  {
    //       if ( encoder1.numberTicks > encoder2.numberTicks) {
    //        motorA (100, 1);
    //        motorB (0, 0);
    //       } else if ( encoder1.numberTicks < encoder2.numberTicks){
    //        motorA (0, 0);
    //        motorB (100, 0);
    //      } else {
    motorA(100, 1);
    motorB(100, 0);
    //      }
  }
  else
  {
    motorA(0, 0);
    motorB(0, 0);
    encoder1.numberTicks = 0;
    encoder2.numberTicks = 0;
    STATE = 0;
  }
}

void motorA(int speed, int direction)
{
  if (direction)
  {
    digitalWrite(DIRA, HIGH);
    ledcWrite(1, 255 - speed);

    // sigmaDeltaWrite(0, 255 - speed);
  }
  else
  {
    digitalWrite(DIRA, LOW);
    //sigmaDeltaWrite(0, speed);
    ledcWrite(1, speed);
  }
}

void motorB(int speed, int direction)
{
  if (direction)
  {
    digitalWrite(DIRB, HIGH);
    //sigmaDeltaWrite(3, 255 - speed);
    ledcWrite(2, 255 - speed);
  }
  else
  {
    digitalWrite(DIRB, LOW);
    //sigmaDeltaWrite(3, speed);
    ledcWrite(2, speed);
  }
}

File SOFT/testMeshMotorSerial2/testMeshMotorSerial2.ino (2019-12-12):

//************************************************************
// this is a simple example that uses the painlessMesh library
//
// 1. sends a silly message to every node on the mesh at a random time between 1 and 5 seconds
// 2. prints anything it receives to Serial.print
//
//
//************************************************************



#include <FastLED.h>
#include "painlessMesh.h"

#define   MESH_PREFIX     "whateverYouLike"
#define   MESH_PASSWORD   "somethingSneaky"
#define   MESH_PORT       5555


#define DATA_PIN    25
#define NUM_LEDS    64

#define PWMA 27
#define DIRA 14
#define PWMB 12
#define DIRB 13
#define PULSE 312

#define   MESH_PREFIX     "whateverYouLike"
#define   MESH_PASSWORD   "somethingSneaky"
#define   MESH_PORT       5555

CRGB leds[NUM_LEDS];// Define the array of leds

unsigned long previousMillis1 = 0;        // will store last time LED was updated
unsigned long previousMillis2 = 0;        // will store last time LED was updated
const long debounce = 500;           // interval at which to blink (milliseconds)
unsigned int led = 0;

int stateMotors = 0;
int stateLeds = 0;

#define NUM_OF_VALUES 10    /** YOU MUST CHANGE THIS ACCORDING TO YOUR PROJECT **/

/** DO NOT REMOVE THESE (SERIAL COMM) **/
int tempValue = 0;
int valueIndex = 0;

/* This is the array of values storing the data from Processing. */
int values[NUM_OF_VALUES];

Scheduler userScheduler; // to control your personal task
painlessMesh  mesh;

String msg = "";

// User stub
void sendMessage() ; // Prototype so PlatformIO doesn't complain

//Task taskSendMessage( TASK_SECOND * 1 , TASK_FOREVER, &sendMessage );

struct Tick {
  const uint8_t PIN;
  uint32_t numberTicks;
  bool tickOn;
};

Tick encoder1 = {16, 0, false};
Tick encoder2 = {17, 0, false};

void IRAM_ATTR isr() {
  encoder1.numberTicks += 1;
  encoder1.tickOn = true;
}
void IRAM_ATTR isr2() {
  encoder2.numberTicks += 1;
  encoder2.tickOn = true;
}


void sendMessageForward() {
  // Serial.println("FORWARD");
  // String msg = "FORWARD";
  mesh.sendBroadcast( msg );
  // taskSendMessage.setInterval( random( TASK_SECOND * 1, TASK_SECOND * 5 ));
}
void sendMessageBackward() {
  //  Serial.println("BACK");
  // String msg = "BACK";
  //  mesh.sendBroadcast( msg );
  // taskSendMessage.setInterval( random( TASK_SECOND * 1, TASK_SECOND * 5 ));
}
void sendMessageRight() {
  //  Serial.println("RIGHT");
  // String msg = "RIGHT";
  //  mesh.sendBroadcast( msg );
  //taskSendMessage.setInterval( random( TASK_SECOND * 1, TASK_SECOND * 5 ));
}
void sendMessageLeft() {
  // Serial.println("LEFT");
  // String msg = "LEFT";
  // mesh.sendBroadcast( msg );
  //taskSendMessage.setInterval( random( TASK_SECOND * 1, TASK_SECOND * 5 ));
}
void sendMessageWhite() {
  // Serial.println("WHITE");
  // String msg = "WHITE";
  // mesh.sendBroadcast( msg );
  //taskSendMessage.setInterval( random( TASK_SECOND * 1, TASK_SECOND * 5 ));
}
void sendMessageBlack() {
  //  Serial.println("BLACK");
  //  String msg = "BLACK";
  //  mesh.sendBroadcast( msg );
  //taskSendMessage.setInterval( random( TASK_SECOND * 1, TASK_SECOND * 5 ));
}
void sendMessageRain() {
  //  Serial.println("RAIN");
  //  String msg = "RAIN";
  // mesh.sendBroadcast( msg );
  //taskSendMessage.setInterval( random( TASK_SECOND * 1, TASK_SECOND * 5 ));
}
// Needed for painless library
void receivedCallback( uint32_t from, String &msg ) {
 // Serial.printf("startHere: Received from %u msg=%s\n", from, msg.c_str());
  if (msg == "MOVEFORWARD") {
    stateMotors = 1;
  } else if (msg == "MOVERIGHT") {
    stateMotors = 2;
  } else if (msg == "MOVELEFT") {
    stateMotors = 3;
  } else if (msg == "MOVEBACKWARD") {
    stateMotors = 4;
  } else if (msg == "LEDBLACK") {
    stateLeds = 1;
  } else if (msg == "LEDWHITE") {
    stateLeds = 2;
  } else if (msg == "LEDRAIN") {
    stateLeds = 3;
  }

  //  leds[led] = CRGB::White; //add an LED
  //  if (led < 64)    led++;
}

void newConnectionCallback(uint32_t nodeId) {
 // Serial.printf("--> startHere: New Connection, nodeId = %u\n", nodeId);
}

void changedConnectionCallback() {
 // Serial.printf("Changed connections\n");
}

void nodeTimeAdjustedCallback(int32_t offset) {
 // Serial.printf("Adjusted time %u. Offset = %d\n", mesh.getNodeTime(), offset);
}
//
//
//void gotTouch1() {
//  // touch1detected = true;
//  if ((millis() - previousMillis1) > debounce) {
//    sendMessageForward();
//    previousMillis1 = millis();
//  }
//}
//
//
//void gotTouch2() {
//  // touch2detected = true;
//  if ((millis() - previousMillis2) > debounce) {
//    sendMessageRight();
//    previousMillis2 = millis();
//  }
//}
//
//void gotTouch3() {
//  // touch2detected = true;
//  if ((millis() - previousMillis2) > debounce) {
//    sendMessageLeft();
//    previousMillis2 = millis();
//  }
//}
//
//void gotTouch4() {
//  // touch2detected = true;
//  if ((millis() - previousMillis2) > debounce) {
//    sendMessageBackward();
//    previousMillis2 = millis();
//  }
//}
void setup() {
  Serial.begin(115200);
  Serial.println("starting...");
  pinMode( 12, OUTPUT);
  pinMode( 13, OUTPUT);
  pinMode( 14, OUTPUT);
  pinMode( 27, OUTPUT);

  FastLED.addLeds<WS2812B, DATA_PIN, RGB>(leds, NUM_LEDS);
  FastLED.setBrightness(30);
  //mesh.setDebugMsgTypes( ERROR | MESH_STATUS | CONNECTION | SYNC | COMMUNICATION | GENERAL | MSG_TYPES | REMOTE ); // all types on
 // mesh.setDebugMsgTypes( ERROR | STARTUP );  // set before init() so that you can see startup messages

  mesh.init( MESH_PREFIX, MESH_PASSWORD, &userScheduler, MESH_PORT );
  mesh.onReceive(&receivedCallback);
  mesh.onNewConnection(&newConnectionCallback);
  mesh.onChangedConnections(&changedConnectionCallback);
  mesh.onNodeTimeAdjusted(&nodeTimeAdjustedCallback);

  // userScheduler.addTask( taskSendMessage );
  // taskSendMessage.enable();
  //  touchAttachInterrupt(T2, gotTouch1, 40);
  //  touchAttachInterrupt(T3, gotTouch2, 40);
  ledcAttachPin(PWMA, 1); // assign RGB led pins to channels
  ledcAttachPin(PWMB, 2);
  // Initialize channels
  // channels 0-15, resolution 1-16 bits, freq limits depend on resolution
  // ledcSetup(uint8_t channel, uint32_t freq, uint8_t resolution_bits);
  ledcSetup(1, 12000, 8); // 12 kHz PWM, 8-bit resolution
  ledcSetup(2, 12000, 8);


  pinMode(encoder1.PIN, INPUT_PULLUP);
  pinMode(encoder2.PIN, INPUT_PULLUP);
  attachInterrupt(encoder1.PIN, isr, FALLING);
  attachInterrupt(encoder2.PIN, isr2, FALLING);
  encoder1.numberTicks = 0;
  encoder2.numberTicks = 0;
}
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

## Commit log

2019-09-26 added Arduino examples
2019-09-26 brought old blueprints over
    [Assembly.f3d, Base.f3d, Emitter Cone.f3d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]
2019-09-26 renamed incoherent files
    [IR.brd, IR.sch, SWARMESH.brd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]
2019-09-26 renamed renders
    [Assembly.f3d, Base.f3d, Emitter Cone.f3d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]
2019-11-02 separated IR in two boards
    [IR.brd, IR.sch, IRRx.brd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]
2019-11-02 updated IRRx
    [IRRx.brd]
2019-11-05 modified IR-TX
    [IRRx.brd, IRTx.brd, IRTx.sch]
2019-11-08 mesh+motor code added
2019-11-08 IR+motor/transistor code
2019-12-12 added leds
2020-06-04 camera calibrated, coordinates converted to real world coordinates
2020-06-05 test board for wireless charging and 3V motors
    [BOTTOM_BRD_v.0.1.0.brd, BOTTOM_BRD_v.0.1.0.csv, BOTTOM_BRD_v.0.1.0.sch]
2020-06-09 multicast motor test
2020-06-10 Updated arduino multicast channels
2020-06-11 oop added to arduino code
2020-06-12 pcb v1.0.1 with pins for sensors and other revisions
    [BOTTOM_BRD_v1.0.1.csv, BOTTOM_BRD_v1.0.1.sch, BOTTOM_BRDv1.0.1.brd]
2020-06-17 Modularization complete
    Need to look for potential bugs (memory leak, etc.) in the future updates
    [Communication.cpp, Locomotion.cpp, Robot.cpp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]
2020-06-17 Reviese driver and slave file
2020-06-18 Simulation revised( direction probelm unsolved)
2020-06-19 Simulation revision
    the first version that works !!!!!!!!
    Improvement expectation:
    1. minimize error (distance + orientation)
    2. simulate the robot better?
    [new_slave.cpp]
2020-06-26 PCB v1.0.2 with ESP32 module, IR sensors, etc
    [BOTTOM_BRD_v.1.0.2_.brd, BOTTOM_BRD_v.1.0.2_.csv, BOTTOM_BRD_v.1.0.2_.sch]
2020-06-30 Updates for board v1.0.2
    [BOTTOM_BRD_v.1.0.2_.brd]
2020-06-30 simple PID added
2020-07-09 collision avoidance file created
    [testCollisionAvoidance.ino]
2020-07-09 updated collision avoidance code
    [testCollisionAvoidance.ino]
2020-07-10 pcb v1.0.3
    [BOTTOM_BRD_v.1.0.5_a.brd, BOTTOM_BRD_v.1.0.5_a.sch]
2020-07-10 pcb v1.0.3 updates
    [BOTTOM_BRD_v.1.0.3.brd, BOTTOM_BRD_v.1.0.3.sch]
2020-07-11 Update pcb v1.0.3b
    [BOTTOM_BRD_v.1.0.3.brd, BOTTOM_BRD_v.1.0.3.sch, BOTTOM_BRD_v.1.0.3b.brd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]
2020-07-12 Update pcb v.1.0.3
    [BOTTOM_BRD_v.1.0.5_c.brd, BOTTOM_BRD_v.1.0.5_c.sch]
2020-07-12 Update pcb v1.0.3
    [BOTTOM_BRD_v.1.0.3.brd, BOTTOM_BRD_v.1.0.3.sch, BOTTOM_BRD_v.1.0.5_c.brd]
2020-07-13 Add wireless charging board
    [WIRELESS_CHARGING_v1.brd, WIRELESS_CHARGING_v1.sch]
2020-07-14 pid course correction added
    [testPID.ino, testRouting.ino]
2020-07-15 PID testbench established
2020-07-16 PID with camera
    (needs to adjust the pid value to make it converge faster)
2020-07-20 pid stable
2020-07-21 PID very stable
2020-07-21 Simulation routing with PID
2020-07-22 PCB v1.0.4 Update
    [BOTTOM_BRD_v.1.0.4.brd, BOTTOM_BRD_v.1.0.4.sch, WIRELESS_CHARGING_v1.brd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]
2020-07-25 collision avoidance rules updated
    [testCollisionAvoidance.ino, testIR_New_Model_.ino]
2020-07-29 front collision avoidance working, combined task assignment
    [testCollisionAvoidance.ino]
2020-11-27 Added PDF of schematic
